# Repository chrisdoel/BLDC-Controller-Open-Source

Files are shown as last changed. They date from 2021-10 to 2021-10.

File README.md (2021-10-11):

# BLDC-Controller-Open-Source
An Open Source BLDC motor speed controller, created from scratch, which supports both sensored and sensorless motors. The full schematic, hardware, code and documentation has been provided.

# Please refer to [Documentation.pdf](/Documentation.pdf) for the complete documentation, theory behding the BLDC controller and construction instructions

# The Schematic
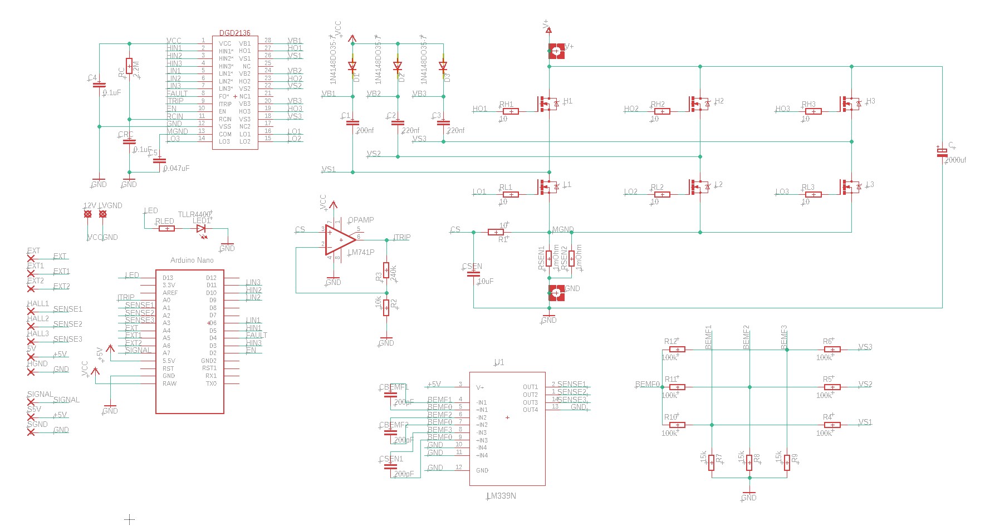
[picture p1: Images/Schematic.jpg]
Schematic
 

# An assembled BLDC controller
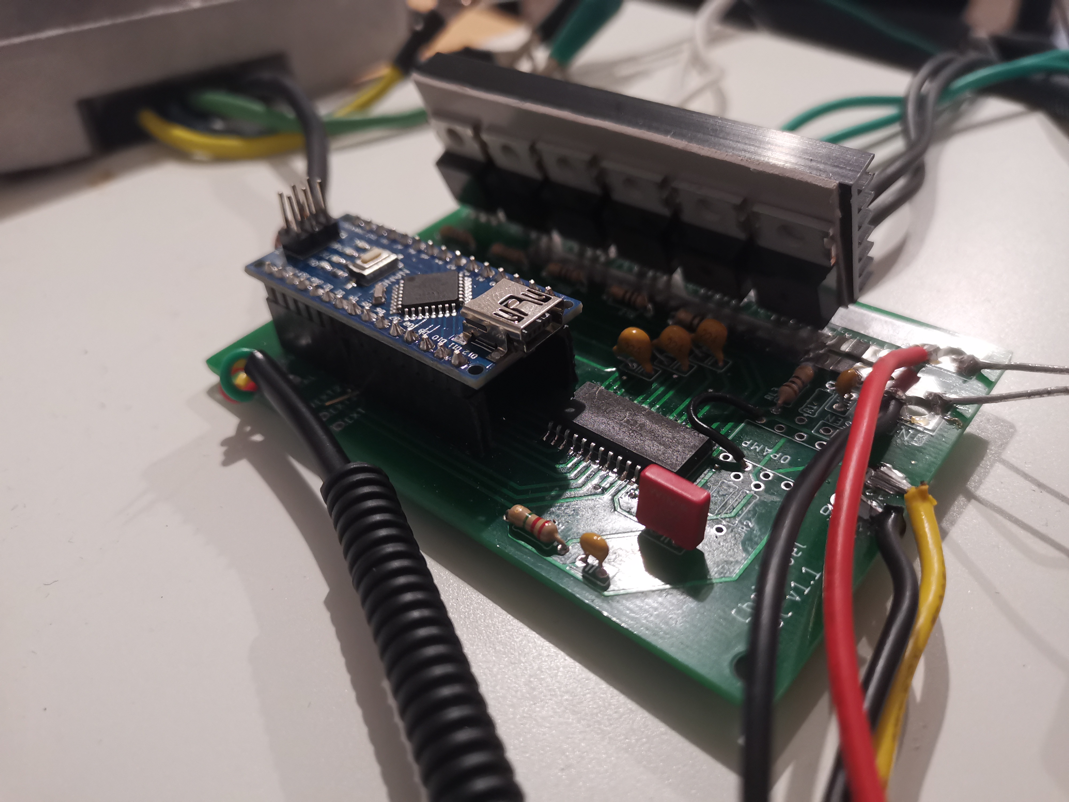
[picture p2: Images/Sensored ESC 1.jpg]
Assembled BLDC controller
 
 
 # The PCB
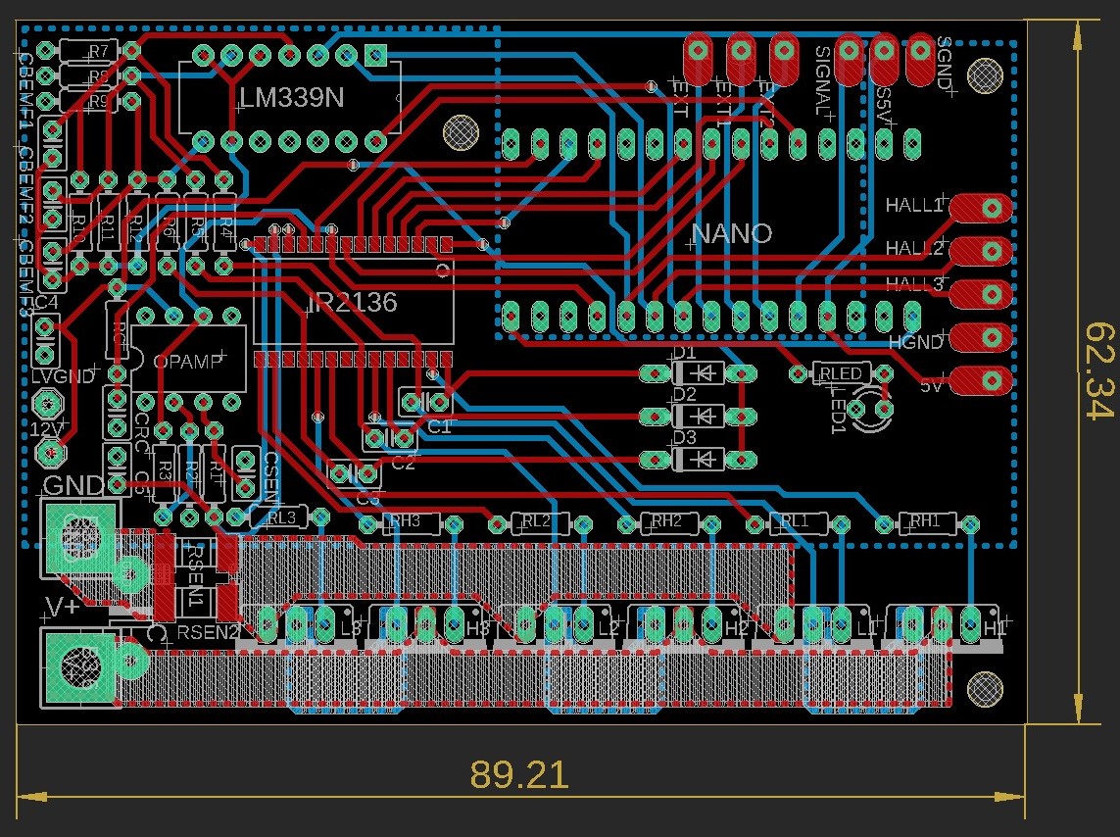
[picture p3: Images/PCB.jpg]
 
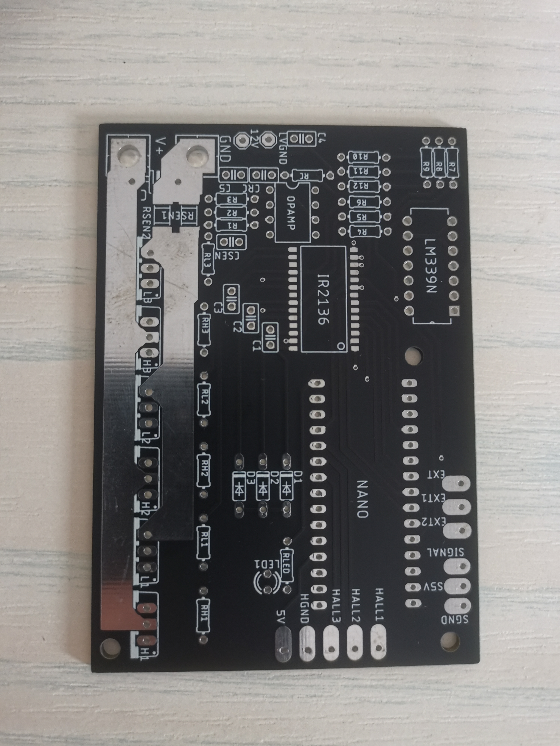
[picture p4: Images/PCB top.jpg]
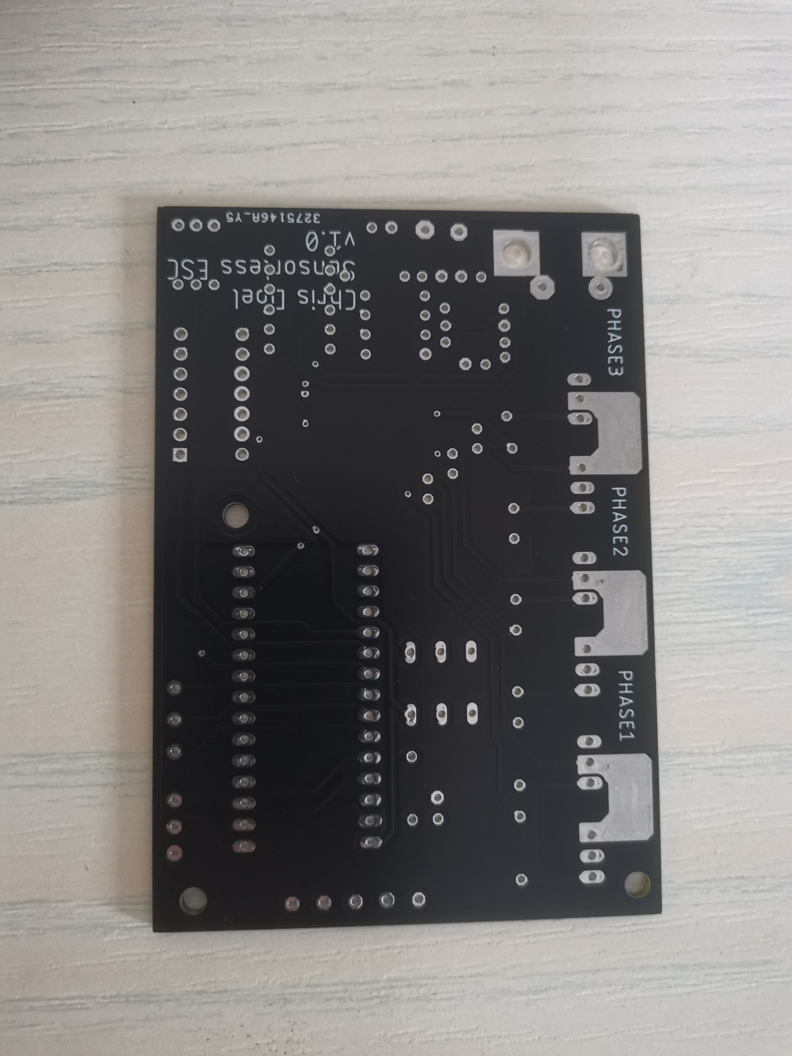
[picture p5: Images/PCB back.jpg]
|  |  |
|:---:|:---:|

# A large sensored motor setup being driven by two BLDC controllers
https://user-images.githubusercontent.com/70950249/136831820-4237cd56-f56c-432a-8c37-596cbc5fa2e3.mp4

# A sensorless motor being driven by the BLDC controller
https://user-images.githubusercontent.com/70950249/136831950-987a125a-ef0f-476e-b4f4-f5f6af1766f3.mp4

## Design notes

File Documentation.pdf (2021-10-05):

## Contents

Designing an open-source brushless motor controller, supporting sensored and sensorless

## Designing an open-source brushless motor controller, supporting sensored and sensorless commutation

Brushless motors are a form of synchronous motors which allow its permanent magnet rotors to rotate without the use of brushes. This therefore enables them to be highly efficient, have a long lifespan and have an impressive weight to power output ratio. However, the drawback of using such motors is that they cannot be powered as simply as brushed dc motors, in which a dc power supply is applied across the motor’s terminals. Brushless motors require a complicated controller,
commonly referred to as an ESC (Electronic speed controller), in order to sequentially switch dc currents across the motors three windings at specific times in order to rotate the motor. Fortunately, due to the widespread availability and cost reduction of microcontrollers and MOSFETS, brushless motor controllers have never been more accessible, especially for hobbyists.

In this documentation I will explain the design decisions and considerations of brushless motor controller with the following requirements:

- It will support sensored commutation by enabling a brushless motor’s hall sensors to be utilised to sense the rotor’s current rotation.
- It will support sensorless commutation by detecting the back EMF generated by the motor windings in order to determine the rotation of the motor’s rotor.
- It will support of an input voltage up to 42v, allowing up to a 10s lithium battery to be used.
- It will support a maximum instantaneous discharge current of around 70 amps.
- It will support a continuous discharge of 30 amps.
- Most of the components will be through hole, enabling a novice electronics hobbyist to easily construct the motor controller.
- The speed controller will be cheaper than most commercial alternatives offering the same specifications (especially when the parts are ordered from Chinese distributors).

## Hardware

### The schematic

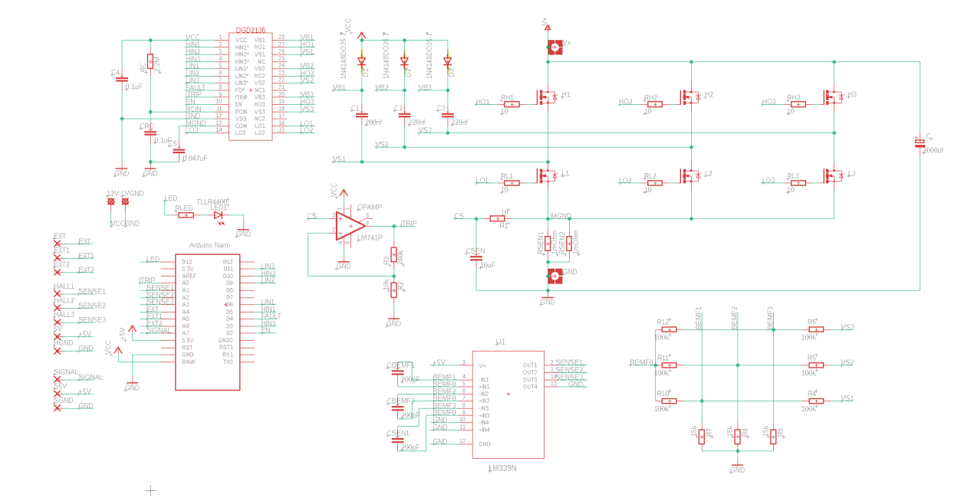
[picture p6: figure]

The speed controller’s schematic can be observed in Figure 1. This includes all the components that will be used in order to construct the speed controller, however certain components can be omitted if only sensored commutation is required (this will be discussed later in the documentation). The schematic consists of four primary areas:

- The microcontroller (an Arduino Nano)
- The triple half bridge MOSFET driver IC (an IR2136 or DGD2136)
- The triple half bridge MOSFET configuration
- The back EMF detection circuitry

### The Tripple half bridge MOSFET configuration

This arrangement of the MOSFETs enables any one of the three motor’s phases to be connected to either the supply voltage or to ground. By connecting one of the phases to the supply, and another to ground, a current is conducted through specific motor windings in a specific direction. The energised windings subsequently apply a force to the motor’s rotor through an attraction/repulsion force with the rotor’s permanent magnets.

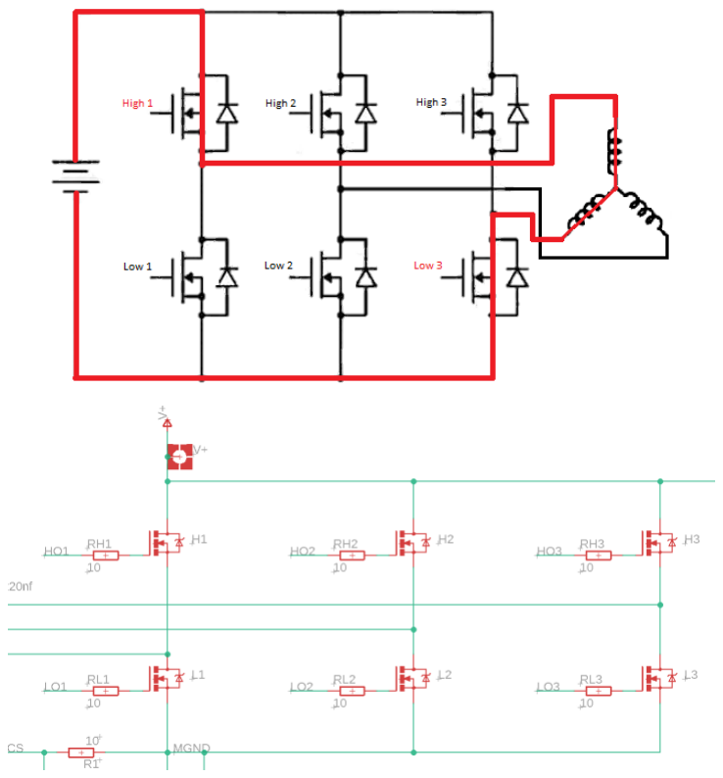
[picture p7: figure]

The MOSFET of choice is the IRF3205. This MOSFET boasts a maximum drain-source voltage of 55v and a maximum continuous drain current of 98A. This MOSFET subsequently supports our voltage requirement of 42v and can handle high continuous currents as long as the MOSFETs are sufficiently cooled.

6 step commutation
In order for a brushless motor to spin most efficiently, the motors windings must be energised in a specific order, and at specific times. This ensures that the motors torque is largest and that the current direction of rotation is maintained. The windings to be energised in order for a four-pole motor to rotate anti-clockwise can be observed in Figure x.

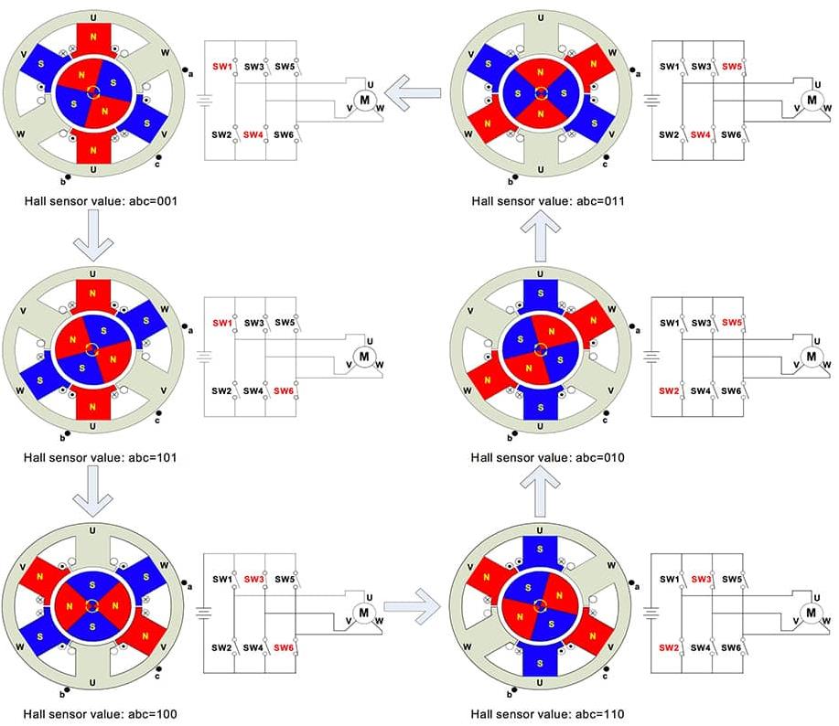
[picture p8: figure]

Figure 1 https://www.digikey.com/en/articles/how-to-power-and-control-brushless-dc-motors

Figure x demonstrates that there are 6 combinations of two MOSFETS to be activated in order for one electrical revolution to be performed (a half revolution for a 4-pole motor). Therefore, if these 6 steps are repeated, the rotor will continuously rotate. In order to adjust the speed of the motor’s rotation, a PWM waveform can be applied to the MOSFETs. The motor’s speed will adjust proportionally to the duty cycle applied to the MOSFETs; which is due to the fact that a motors speed is proportional to the average voltage applied across the motors windings.

Sensored commutation theory
As explored above, the position of the motor’s rotor is required in order to determine the two MOSFETs to be switched. One common approach of detecting the rotor’s current rotation is through the use of hall sensors integrated within the motor. These hall sensors are spaced either 60 or 120 degrees around the motors stator and detect the presence of the magnetic field from the motor’s rotor. The majority of the hall sensors output a 5v logic signal in order to indicate the magnetic pole that is present. These hall sensors are strategically spaced in order to output three logic signals which correlate to the windings that need to be energised in order to continue the motors rotation. A table showing the windings to be excited with the corresponding hall signals can be observed in Figure x.

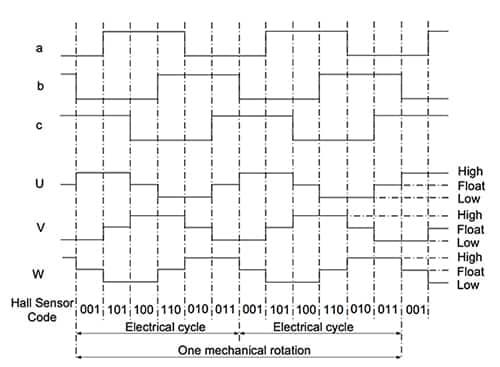
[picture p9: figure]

Sensorless commutation theory
The sensored approach highlighted above however has the disadvantage of adding additional cost and complexity to the motor. To mitigate this downside, an alternative method of detecting the motors rotation has been devised and is used extensively with hobbyist motors. This sensorless commutation approach relies on the fact that as the rotor rotates after a current is applied to two of the motor’s phases, the rotors permanent magnets pass by the motors un-excited winding. This action of passing a permanent magnet near a winding results in the generation of an EMF. As this winding is currently un-energised, the EMF can be sensed by the speed controller and can be correlated to the current position of the rotor. The waveform generated by the back EMF can be observed in Figure x below:

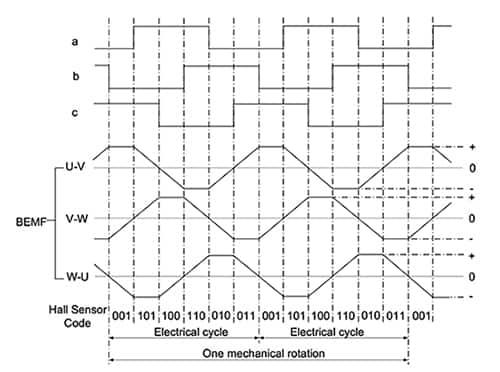
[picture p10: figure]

This diagram demonstrates that the step of the 6-step commutation is to be advanced when the BEMF of the floating phase crosses the zero point. Subsequently, this zero-crossing event can be monitored for each specific step of the 6-step commutation in order to continuously rotate the rotor.

This commutation method however consists of its own downsides. The primary downside is that the magnitude of the BEMF waveform is proportional to the rate of change of the magnetic field across the motors winding. This therefore means that at a low rotational speed, the BEMF waveform is hard to detect; and at a standstill there is no BEMF waveform at all. Therefore, the windings need to be initially energised in a sequence that is not correlated to the rotors position, until enough movement is created for a BEMF signal to be observed.

Current sensing
In order for the current draw of the BLDC controller to be measured, a shunt resistor is utilised. The voltage across this shunt resistor is amplified and measured in order to accurately determine the amount of current passing through the motor. This ensures that in situations in which the motor has stalled or is drawing more current than the BLDC controller is designed for, the PWM signal applied to the MOSFETs can be stopped in order to prevent damage. A simple non-inverting amplifier allows the small voltage across the shunt resistor to be amplified to a more appropriate voltage range for interpretation for a microcontroller or IC.

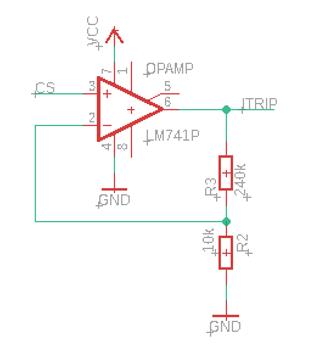
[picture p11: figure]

### Bootstrapping

Theory
Each half bridge utilises two N channel MOSFETs. Initially it may seem counter intuitive to utilise two N channel FETs due to the fact that the high side MOSFET would need a very high gate voltage, relative to the circuits ground, in order to sufficiently activate the MOSFET. This is due to the fact that there will be a voltage across the motor’s windings, therefore the high side MOSFET will require a Vgs (with respect to ground) which is equal to the MOSFETS saturation voltage plus this voltage drop across the windings. Therefore, the high side MOSFETs gate voltage must be higher than its drain voltage, meaning that this voltage will most likely have to be provided from a source external to this circuit. An alternative to using two N channel MOSFETs would be to use an N channel for the low side MOSFET and a P channel for the high side. However, using only N channel MOSFETs not only reduces the cost of the circuitry, but it also results in a reduction of the losses due to the inherent attribute of P channel MOSFETs consisting of a higher Rdson resistance.

A solution which enables the utilisation of two N channel MOSFETs in a half bridge configuration is referred to as MOSFET bootstrapping. Bootstrapping enables a capacitor, connected between the circuits supply and the high side MOSFETs drain, to be charged when the low side MOSFET is activated. The voltage across this charged capacitor can then be used in order to provide a sufficient voltage (relative to the high side MOSFETs source) to the gate of the high side MOSFET.

Implementation

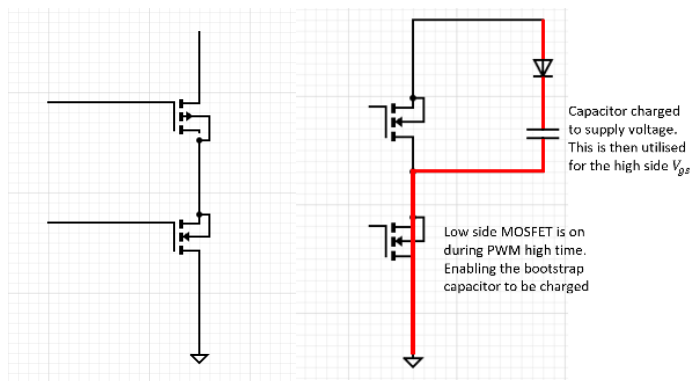
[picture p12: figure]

An 1N1418 diode has been used as the bootstrap diode due to its high speeds; this is necessary as the bootstrap capacitor will need to be sufficiently charged within the very small timeframe of the low side MOSFETs PWM on time.

A specific bootstrap capacitance is required to be tailored around the PWM frequency used to drive the MOSFETS and the MOSFETS gate capacitance.

The charge that must be stored by the bootstrap capacitor is expressed in the following equation:

QCB = QG + (tLmax × IB)

Where:

- QCB is the total charge to be stored.
- QG is the MOSFETs typical gate capacitance.
- tLmax is the maximum time that the high side MOSFET PWM waveform will be high.
- IB is the maximum quiescent supply current stated in the MOSFET driver’s datasheet.

In the case of this speed controller:

- The IRF3205 has a gate charge of 146nC, therefore QCB = 146nC
- A 31kHz PWM frequency is utilised so tLmax = 32μs

- The IR2136’s maximum quiescent Vbs supply current is IB = 70 × 10⁻⁶

QCB = 147 × 10⁻⁹ + (32 × 10⁻⁶ × 70 × 10⁻⁶

) = 1.4924 × 10⁻⁷

Finally, we need to tailor the value of CB around the maximum allowable ripple. In this case I will allow a 5% ripple of the 12v supply.

CB ≥

QCB
∆V
1.4924 × 10⁻⁷
∆V

= 248 nF

### The MOSFET driver IC

The IR2136 enables the Arduino’s 6 PWM signals to be utilised in order to switch the 6 MOSFETs within the triple half bridge configuration. Using a MOSFET driver is preferable to simply using the Arduino’s logic level PWM signals due to the fact that the Arduinos low voltage and high impedance output results in considerably slower switching times, consequentially causing MOSFET heat losses. This IC supports a supply voltage of 10-20v; I will be powering it used an automotive switching dc regulator with an output of 12v.

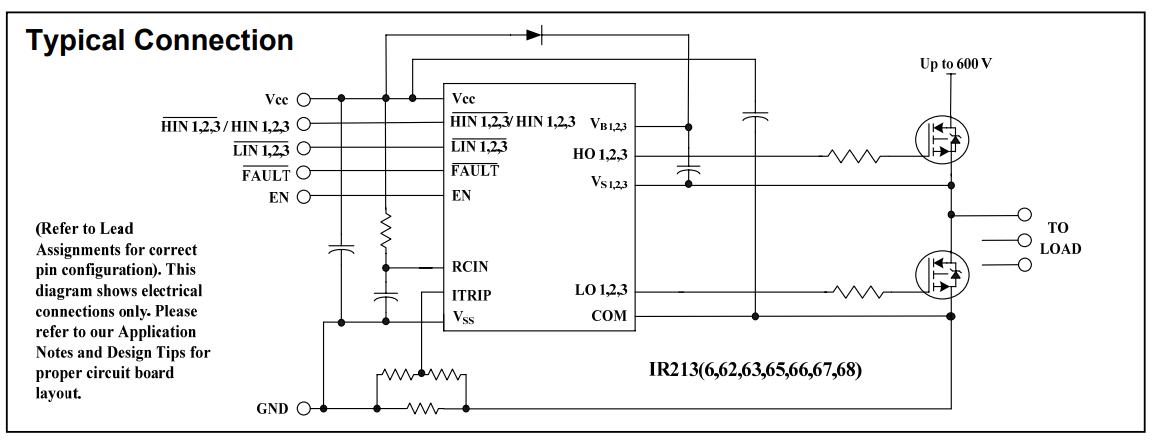
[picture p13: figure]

Pin descriptions
Pins
HIN1, 2, 3 LIN1, 2, 3 | The HIN pins receive the PWM signal for the high side MOSFETs of each half bridge and the LIN pins receive the PWM signals for the low side FETs. Depending on the variant of the ir2136, these inputs can be inverted. In my case I am using the ir2136S which has both the HIN and LIN signals inverted.
FAULT | The fault pin indicates an overcurrent or undervoltage event in the form of an open drain signal. This is connected to the Arduinos digital input pin 4 which is in pullup mode. The fault signal is inverted.
RCIN | A pin which connects to a series RC network in order to define the amount of time for the FAULT signal to clear. This time is approximately equal to R*C.
ITRIP | This is the analog input for the overcurrent detection. When the voltage at this pin exceeds 4.3V the chips operation is halted and the FAULT signal output. For this application a simple amplifier is used in order to amplify the voltage drop across the shunt resistor. The gain of the amplifier is strategically chosen in order to result in a 4.3v output when the maximum current is reached.
EN | A logic input to enable the ir2136 to operate.

HO1, 2, 3 LO1, 2, 3 | The output pins in order to drive the high and low side MOSFETs. This output logic signal will consist of the same PWM waveform applied to its corresponding input pin, however depending on the ir2136 variant it may be inverted.
VB1, 2, 3 VS1, 2, 3 | The VB pin connects to the node attaching the bootstrap capacitor to the supply voltage. The VS pin connects to the node connecting the bootstrap capacitor to the drain of the high side MOSFET. These pins enable the bootstrap capacitor to be charged and discharged in order to drive the high side N channel MOSFET.

Deadtime
The IC provides a typical dead time value of 290 nanoseconds. This means that there will be a 290ns delay between one of a half bridges MOSFETs being turned off and the other MOSFET being turned on. This minimises the risk of both MOSFETs being activated at the same time, which would result in a direct short circuit between the supply and ground through both MOSFETs.

### Sensorless commutation hardware

An effective but simple method of measuring the BEMF zero crossing events (highlighted in Sensorless Commutation Theory) is to use a resistor network composed of nine resistors, this can be observed in the Figure below.

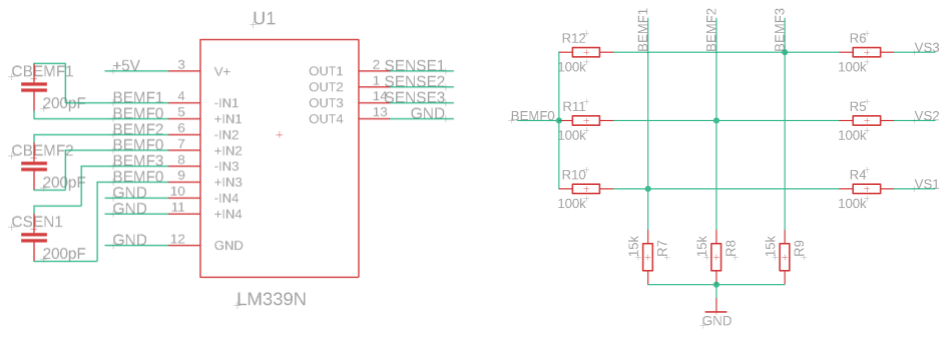
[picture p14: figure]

Resistors R6, R5 and R4 are connected to the three motor phases. R7, R8 and R9 create a potential divider with R6, R5 and R4, allowing the voltage from each phase to be attenuated to within a 5-volt range. The attenuated voltages are then combined at the BEMF0 node in order to simulate the motors neutral point (a point where a brushless motors phases join internally when in a Y configuration but is usually inaccessible externally). This point now allows us to sense the voltage across each of the motors windings by measuring the phase voltage to this virtual neutral point. This subsequently means that the BEMF induced within the motor’s windings can be detected. As we are only concerned as to whether a BEMF zero crossing event has occurred, an LM339N 4 channel comparator has been utilized. This comparator outputs a logic signal corresponding to whether the voltage across a phase winding is above or below the virtual neutral voltage. Therefore, by inspecting these signals for a change in states, we can determine that a BEMF crossing event has occurred for a particular phase, and therefore advance the commutation sequence step.

A capacitor is required in order to smooth each attenuated voltage signal in order to reduce any high frequency noise superimposed on the BEMF signal. Any superimposed noise can cause lots of bouncing and erroneous state changes to be detected. This capacitor is connected between the virtual neutral point and each of the phases and consists of a value of 200 pF.

### The microcontroller

The brains of the speed controller are in the form of an Arduino Nano, which is a breadboard-friendly board based on the ATMega328 microcontroller. These boards are widely used within the hobbyist electronic space and are incredibly cheap, especially when purchased in the form of a third-party clone. This microcontroller typically runs at 16MHz which is relatively slow compared to other microcontrollers used to control BLDC speed controllers. Therefore, the nano must be programmed as efficiently as possible to make use of the limited processing power. As a result, most of the advantages provided by the Arduino framework are not utilised and port/register manipulation was an effective programming tool.

Timer utilisation and timekeeping
The ATMega328 only has three hardware timers, all of which are used to generate the PWM signal for two of the 6 PWM pins. As the BLDC controller requires 6 PWM signals to the MOSFETs, all of the timers were already being used and therefore I could not have a timer dedicated to the task of timekeeping. The PWM frequency is set to 32kHz, and the timer resolution restricted to 8 bits, subsequently meaning that the timers value would increment and overflow extremely fast, far too fast to utilise the timer’s values for timekeeping. This issue was mitigated by adding an overflow interrupt to one of the timers, in which a global 16-bit integer is incremented at each overflow event, resultantly giving me a 32kHz timer. This timer variable would take around two seconds to overflow which is a perfectly reasonable time range.

The main requirement for timekeeping is so that there is a timeout for the speed controller being in one of the commutation steps. If the controller is in one of the commutation steps for an unordinary amount of time, then this suggests that the motor has stalled, or some other fault has occurred. As a result, the PWM duty cycle for the MOSFETs needs to be set to 0 in order to prevent a sustained high current draw. This timeout value is set to 1072 clocks of the make-shift timer, corresponding to around 32 milliseconds.

Generating the PWM waveform
The PWM frequency used to generate the PWM waveform for the MOSFETs is 32KHz. This PWM frequency is rather high, however it means that the speed controller will happily support motors that consist of high pole counts and spin at a high RPM. By default, the Arduino supports a PWM frequency of 500hz. This frequency is far too small for this application, therefore it needed to be increased by manipulating the registers that determine the timers prescaling.

The prescaler was set to 1 and the timers resolution set to 8 bits, meaning that the overflow frequency is ¹⁶⁰⁰⁰⁰⁰⁰
256

= 62500. Phase correct PWM was then applied by manipulating the timer mode registers. This means that the timer would first increment until its maximum value before decrementing back to its lowest value, resulting in a PWM frequency of 31250. The two Output Compare Registers are then set in order to toggle the PWM pins output at each matching comparison; thus, generating a PWM waveform which can be observed in the figure below.

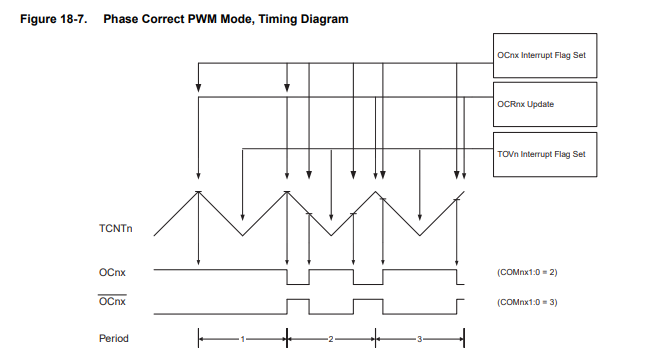
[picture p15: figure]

Sensored logic flowchart
The logic for sensored operation is rather simple. The throttle is sampled every 20 milliseconds, in which the throttle is mapped to an 8-bit range before being assigned as the PWM duty cycle. The hall sensors logic levels are read before being utilised in order to determine the commutation step that should be currently applied. A timeout is used in order to ensure that a commutation step is not applied for too long, as this suggests the motor has been stalled or the wrong commutation step is being applied.

Sensorless logic flow chart
The sensorless logic is slightly more complex. As the magnitude of the BEMF signal is proportional to the speed in which the motor is running, this means that there will not be any way to determine the rotors position while stationary. As a result, we are required to perform open loop commutation in order to get the motor to briefly move and generate a BEMF signal. As can be observed in the flowchart, the six-step commutation sequence is performed, with 5 millisecond intervals, a total of 12 times. Once this has been completed, the microcontroller attempts to detect a phase 3 BEMF event (which would be the next BEMF event to be observed). If this is successfully detected then this means that the rotors position has been determined and we can perform closed loop, sensorless commutation.

Once the rotor is spinning, the sensorless commutation is rather similar to sensored commutation. During each commutation step, the microcontroller will monitor the BEMF channels until it detects the expected rise or fall signal for that specific commutation step. This indicates that the commutation step is to be advanced, and the process is continued.

## Reflections, issues and improvements

To reflect on the speed controller as a whole, I am very satisfied with the outcome, and I believe that it meets all of my initially stated requirements. I have utilised this brushless speed controller to drive a large range of brushless motors (from small hobbyist sensorless motors to huge 1.5kW+ rated sensored motors). The sensorless commutation has greatly exceeded my expectations and is able to very reliably start and continuously rotate sensorless brusless motors. I am very pleased with the PCB and the general package of the final product, especially as the PCB is able to be utilised for both sensored and sensorless applications.

I have occasionally run into issues where two of the MOSFETs from a single phase fail and develop a short. This has only occurred when running with relatively high loads and at voltages above 36v. I believe that this issue could be a result of possibly large BEMF voltage spikes; of which are exceeding the ratings of the MOSFETs and resulting in its failure. Another possible cause of its failure could be an insufficient bootstrap capacitor, in which it is not able to contain enough charge to fully open the gate of the high side MOSFET. I will continue to investigate and rectify any issues found with this speed controller.

If I were to completely resign this speed controller then I would definitely utilise another microcontroller. As briefly explored in this documentation, the AtMega328p is not a very suitable microcontroller for this role. The primary reasoning behind this would be its limitation on speed and the availability of timers. I would also design the PCB to be able to support multiple parallel
MOSFETs for each side of each phase. Such a feature would result in a dramatic reduction of
MOSFET heating and would enable the speed controller to tolerate much higher currents. This would be due to the fact that the total MOSFET resistance would half and any heat as a result of this resistance would be distributed over multiple MOSFET packages.

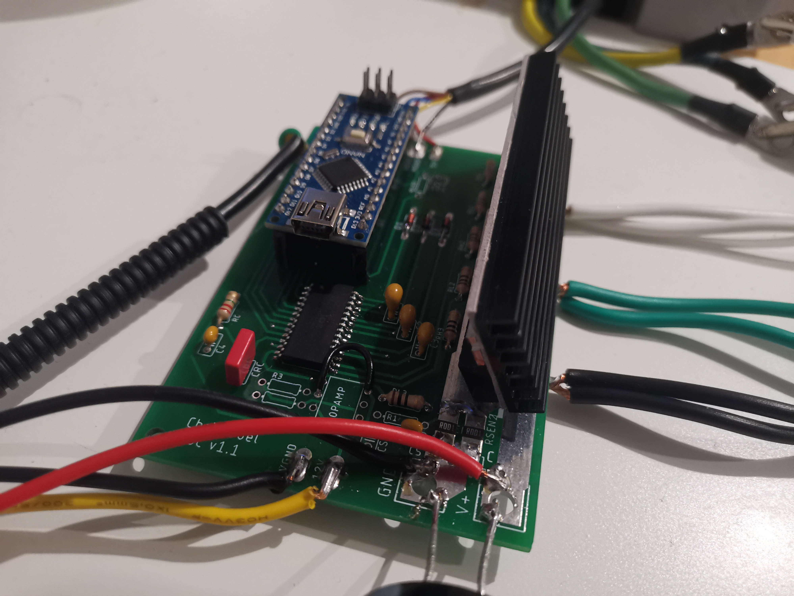
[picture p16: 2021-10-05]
Images/Sensored ESC 2.jpg

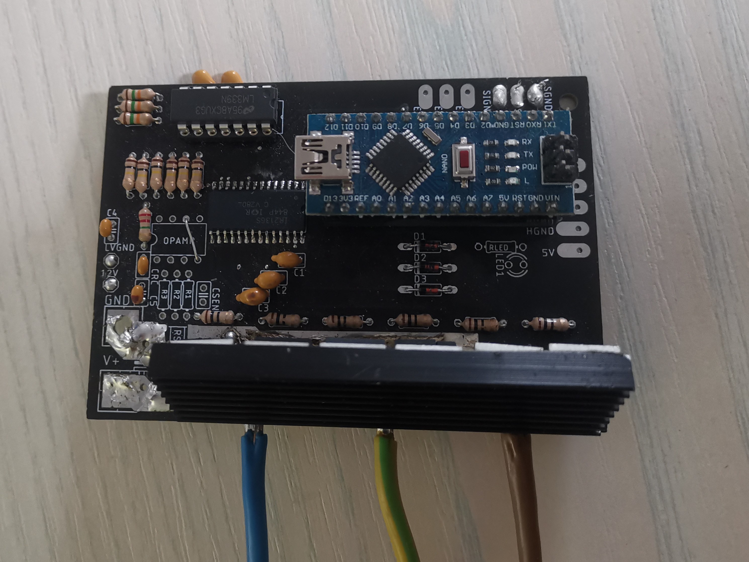
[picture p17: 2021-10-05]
Images/Sensorless ESC.jpg

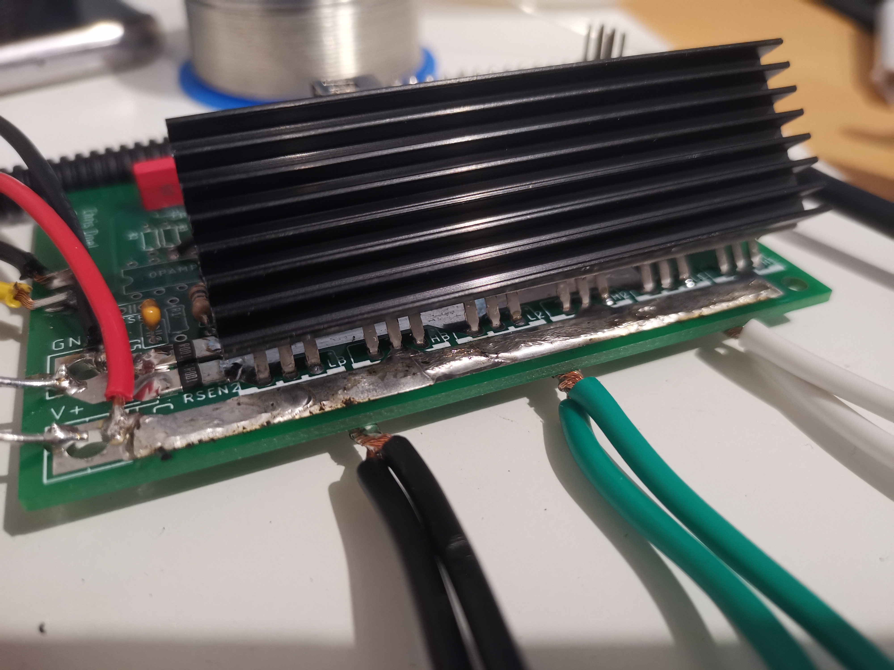
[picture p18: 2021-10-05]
Images/Copper wick added.jpg

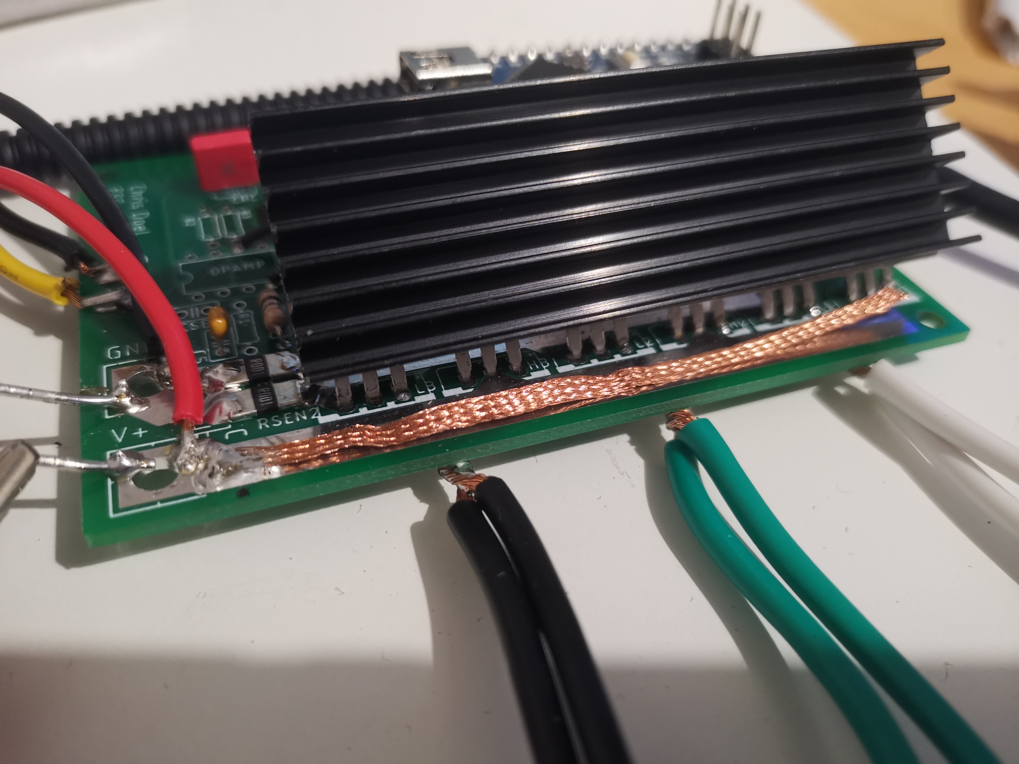
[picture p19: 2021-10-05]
Images/Adding copper wick.jpg

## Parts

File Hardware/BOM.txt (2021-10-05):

For only hall sensor operation:
1x ir2136s
6x mosfets (for cheap high current use IRF3205)
6x 10 Ohm resistor
3x 220nF (This depends heavily on the choice of mosfet and will have to be recalucated if using different mosfets, see bootstrap capacitor calculation image)
2x 0.1uf
1x 0.047uf (can be swapped for another 0.1uf)
1x 2.2M Ohm

For current limitation
2x 2512 3W 1mOhm smd resisitors
741 op amp
1x 10uf
an input and feedback resistor for required gain, for example:
>Voltage drop across the two shunt resistors in parallel at 40 amp is 40*0.0005 = 0.02v
>The ir2316 cuts out when ITRIP exceeds a voltage of 0.5v
>Therefore, if our max current was 40 amp, we want a non inverting gain of 25

Extra components for sensorless operation:
1x 10uf
3x 15k Ohm
6x 100k Ohm
1x LM339N
3x 200pf

You will obviously need an arduino nano
You will need a buck converter module capable of stepping down the input voltage to 12v and ideally able to provide 1 amp
The input is simply a potentiometer, a pulldown resistor with a high value is recommended to prevent noise being registered as throttle input if the throttle is disconnected

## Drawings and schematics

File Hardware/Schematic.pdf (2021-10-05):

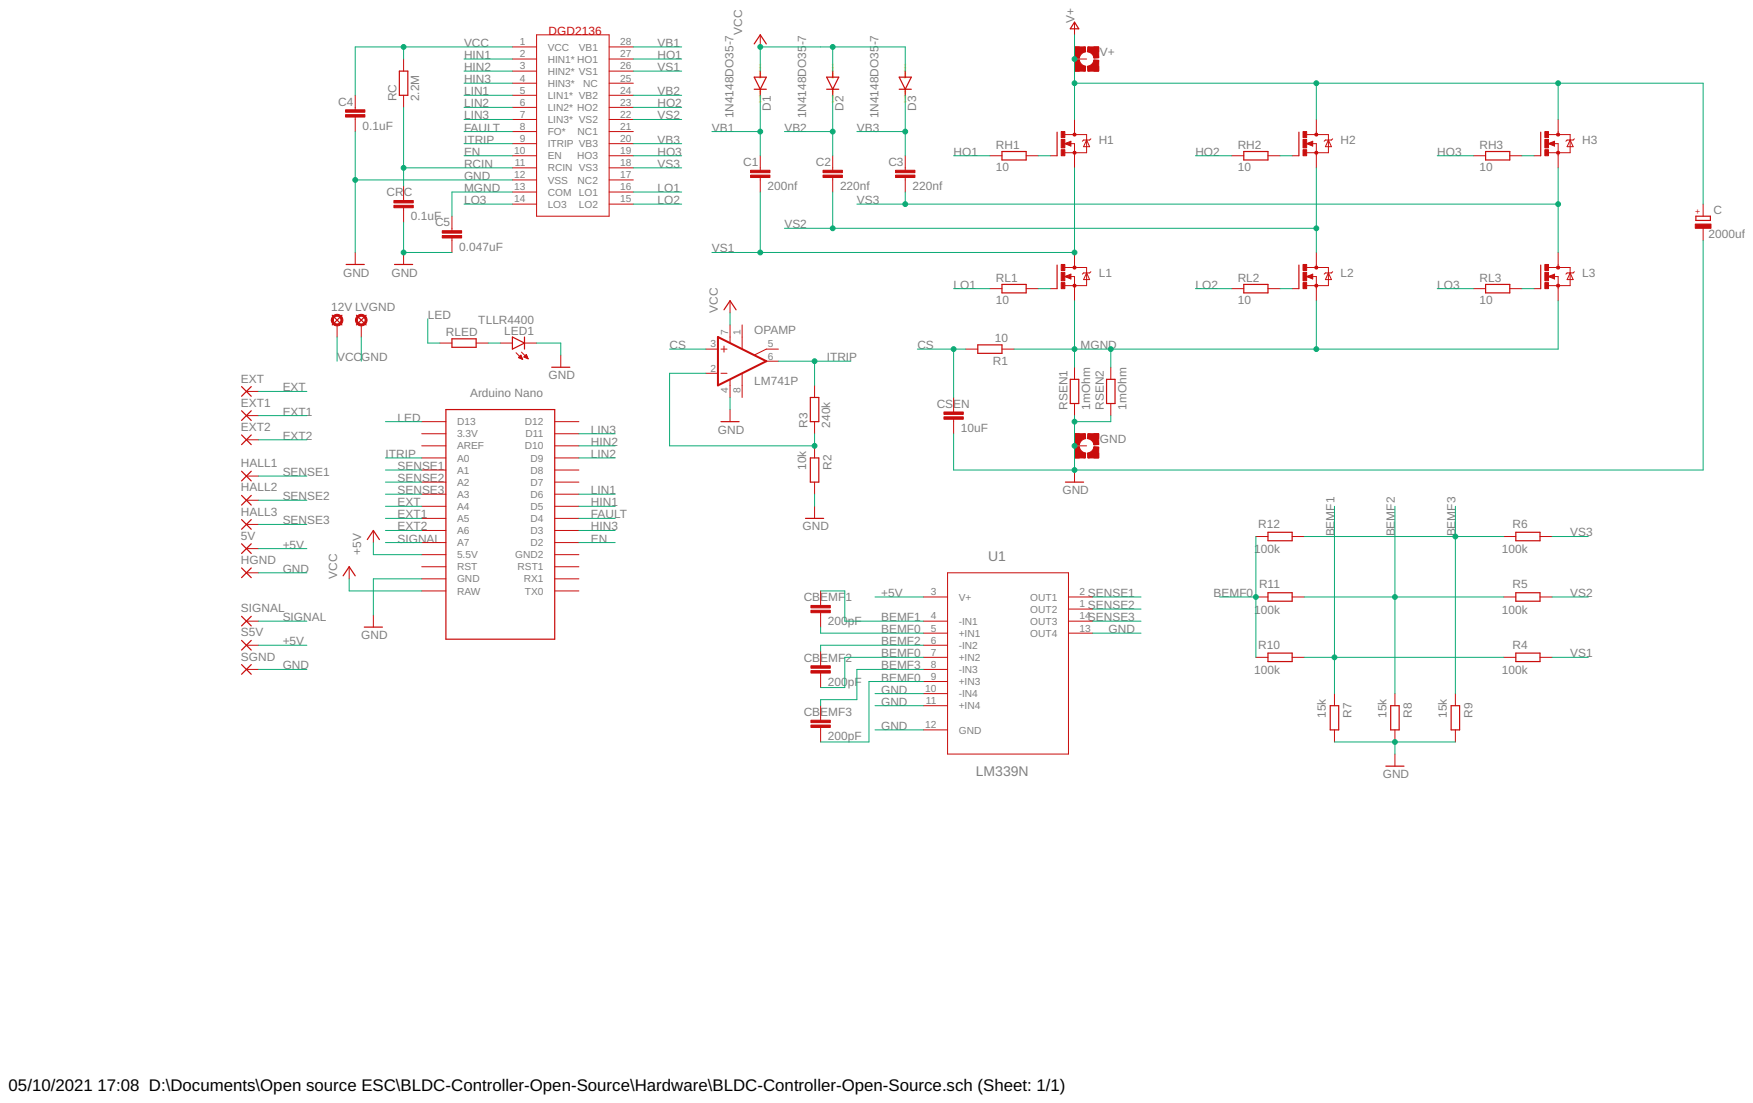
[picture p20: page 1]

05/10/2021 17:08 D:\Documents\Open source ESC\BLDC-Controller-Open-Source\Hardware\BLDC-Controller-Open-Source.sch (Sheet: 1/1)

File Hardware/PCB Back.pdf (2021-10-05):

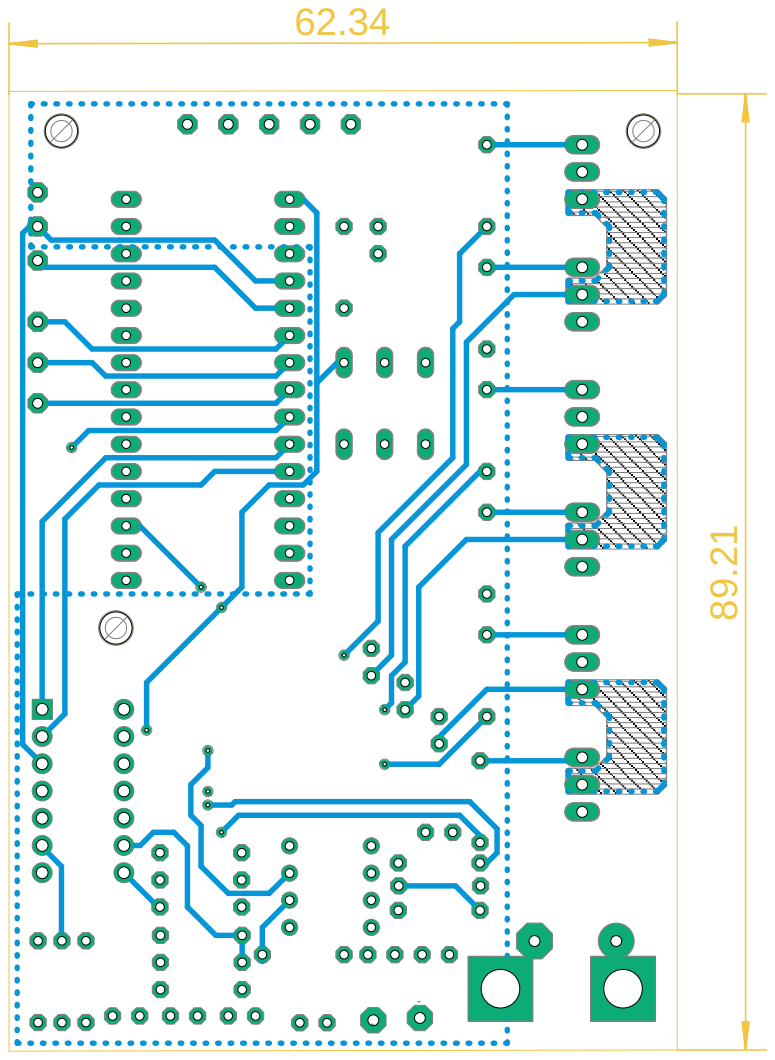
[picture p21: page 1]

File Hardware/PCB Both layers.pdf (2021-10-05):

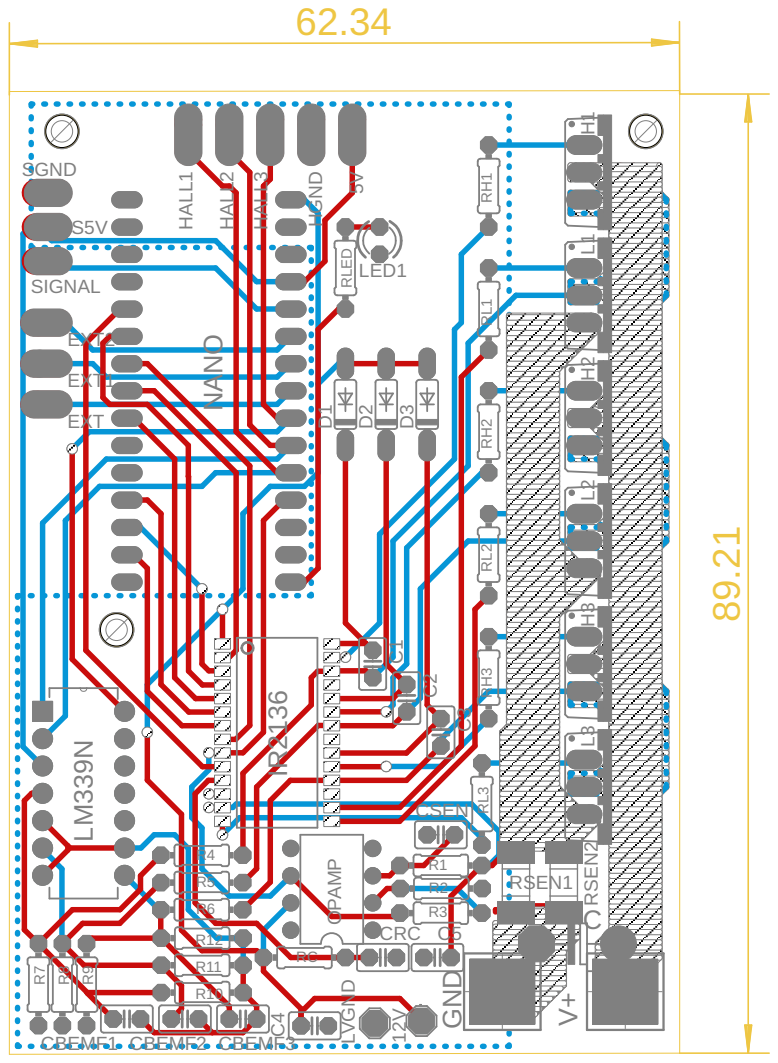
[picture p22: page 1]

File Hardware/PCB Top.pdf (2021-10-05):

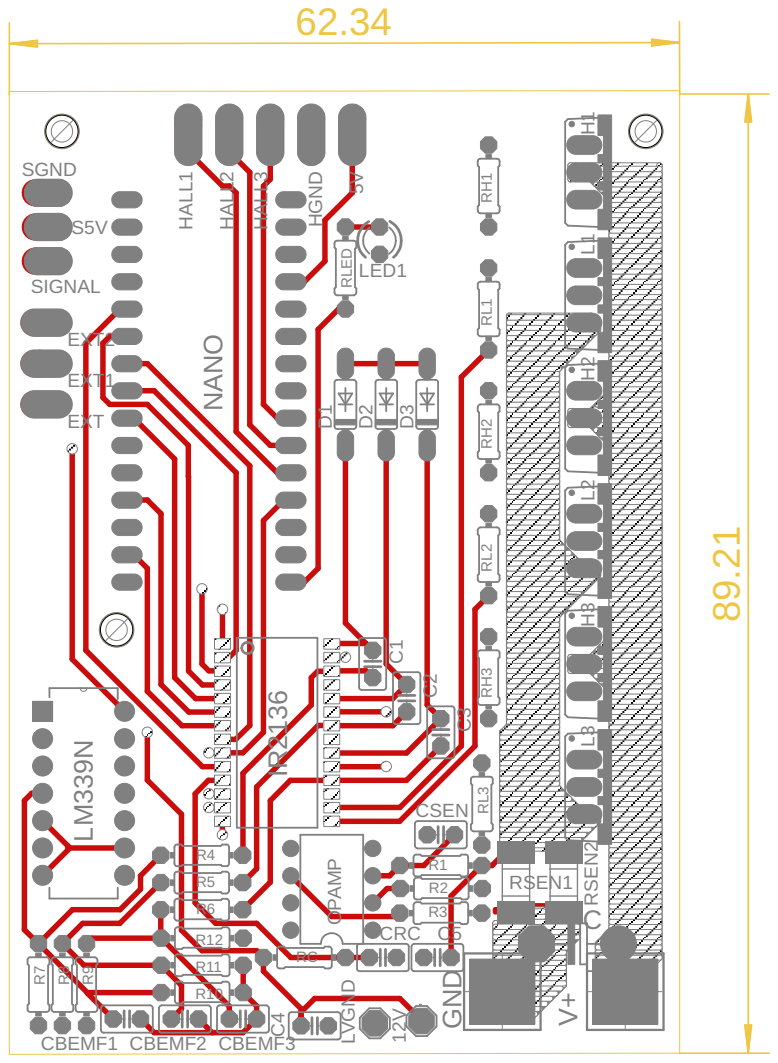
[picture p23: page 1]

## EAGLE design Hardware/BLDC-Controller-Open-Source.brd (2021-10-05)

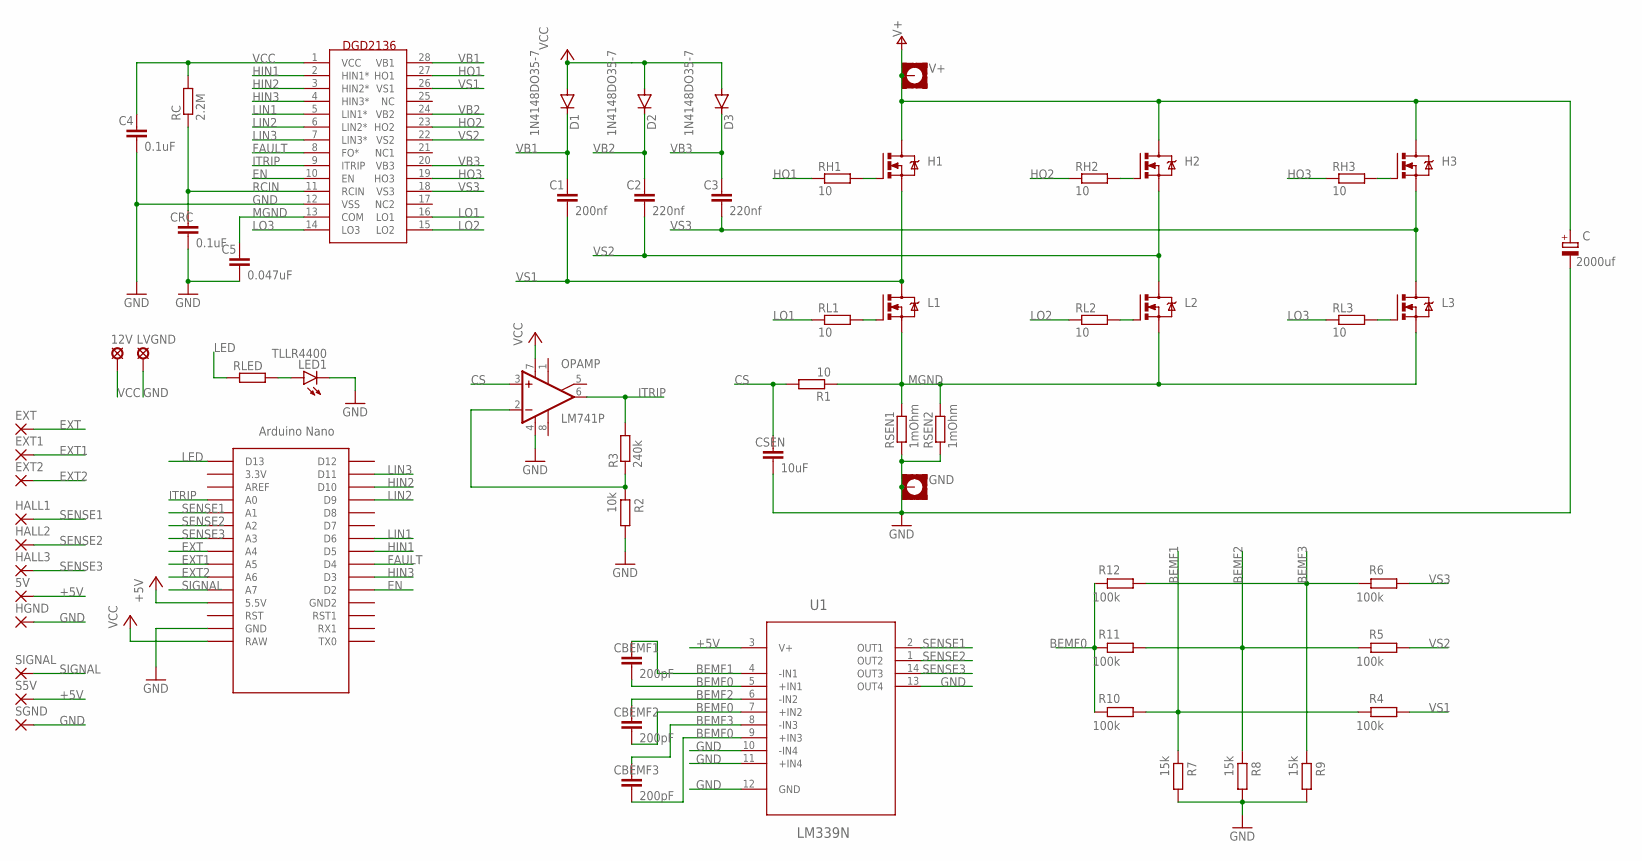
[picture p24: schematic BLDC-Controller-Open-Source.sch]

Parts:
5V: 1,6/0,9
12V: MCS10B
C: 2000uf; E7,5-16
C1: 200nf; C025-025X050
C2, C3: 220nf; C025-025X050
C4: 0.1uF; C025-025X050
C5: 0.047uF; C025-025X050
CBEMF1, CBEMF2, CBEMF3: 200pF; C025-025X050
CRC: 0.1uF; C025-025X050
CSEN: 10uF; C025-025X050
D1, D2, D3: 1N4148DO35-7; DO35-7
EXT, EXT1, EXT2: 1,6/0,9
GND: MOUNT-PAD-SQUARE3.6; 3,6-PAD-SQUARE
H1, H2, H3: IRF540; TO220BV
HALL1, HALL2, HALL3: 1,6/0,9
HGND: 1,6/0,9
L1, L2, L3: IRF540; TO220BV
LED1: TLLR4400; LED3MM
LVGND: MCS10B
OPAMP: LM741P; DIL08
R1: 10; 0204/7
R2: 10k; 0204/7
R3: 240k; 0204/7
R4, R5, R6, R10, R11, R12: 100k; 0204/7
R7, R8, R9: 15k; 0204/7
RC: 2.2M; 0204/7
RH1, RH2, RH3: 10; 0204/7
RL1, RL2, RL3: 10; 0204/7
RLED: R-EU_0204/7; 0204/7
RSEN1, RSEN2: 1mOhm; R2512
S5V: 1,6/0,9
SGND: 1,6/0,9
SIGNAL: 1,6/0,9
U1: LM339N; DIP254P762X508-14
U$1: NANO
U$2: DGD2136
V+: MOUNT-PAD-SQUARE3.6; 3,6-PAD-SQUARE

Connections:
+5V: 5V.1, S5V.1, U1.3 (V+), U$1.5V (5.5V)
BEMF0: CBEMF1.2, CBEMF2.2, CBEMF3.2, R10.2, R11.2, R12.2, U1.5 (+IN1), U1.7 (+IN2), U1.9 (+IN3)
BEMF1: CBEMF1.1, R4.2, R7.2, R10.1, U1.4 (-IN1)
BEMF2: CBEMF2.1, R5.2, R8.2, R11.1, U1.6 (-IN2)
BEMF3: CBEMF3.1, R6.2, R9.2, R12.1, U1.8 (-IN3)
CS: CSEN.1, OPAMP.3 (+IN), R1.2
EN: U$1.D2, U$2.10 (EN)
EXT: EXT.1, U$1.A4
EXT1: EXT1.1, U$1.A5
EXT2: EXT2.1, U$1.A6
FAULT: U$1.D4, U$2.8 (FO*)
GND: C.-, C4.2, C5.2, CRC.2, CSEN.2, GND.B3,6, HGND.1, LED1.K (C), LVGND.MP, OPAMP.4 (V-), R2.1, R7.1, R8.1, R9.1, RSEN1.1, RSEN2.1, SGND.1, U1.10 (-IN4), U1.11 (+IN4), U1.12 (GND), U1.13 (OUT4), U$1.GND, U$2.12 (VSS)
HIN1: U$1.D5, U$2.2 (HIN1*)
HIN2: U$1.D10, U$2.3 (HIN2*)
HIN3: U$1.D3, U$2.4 (HIN3*)
HO1: RH1.1, U$2.27 (HO1)
HO2: RH2.1, U$2.23 (HO2)
HO3: RH3.1, U$2.19 (HO3)
ITRIP: OPAMP.6 (OUT), R3.2, U$1.A0, U$2.9 (ITRIP)
LED: RLED.1, U$1.D13
LIN1: U$1.D6, U$2.5 (LIN1*)
LIN2: U$1.D9, U$2.6 (LIN2*)
LIN3: U$1.D11, U$2.7 (LIN3*)
LO1: RL1.1, U$2.16 (LO1)
LO2: RL2.1, U$2.15 (LO2)
LO3: RL3.1, U$2.14 (LO3)
MGND: C5.1, L1.S, L2.S, L3.S, R1.1, RSEN1.2, RSEN2.2, U$2.13 (COM)
unnamed: L3.G, RL3.2
unnamed: H3.G, RH3.2
unnamed: L1.G, RL1.2
unnamed: L2.G, RL2.2
unnamed: H2.G, RH2.2
unnamed: H1.G, RH1.2
unnamed: OPAMP.2 (-IN), R2.2, R3.1
unnamed: LED1.A, RLED.2
RCIN: CRC.1, RC.1, U$2.11 (RCIN)
SENSE1: HALL1.1, U1.2 (OUT1), U$1.A1
SENSE2: HALL2.1, U1.1 (OUT2), U$1.A2
SENSE3: HALL3.1, U1.14 (OUT3), U$1.A3
SIGNAL: SIGNAL.1, U$1.A7
V+: C.+, H1.D, H2.D, H3.D, V+.B3,6
VB1: C1.1, D1.C, U$2.28 (VB1)
VB2: C2.1, D2.C, U$2.24 (VB2)
VB3: C3.1, D3.C, U$2.20 (VB3)
VCC: 12V.MP, C4.1, D1.A, D2.A, D3.A, OPAMP.7 (V+), RC.2, U$1.RAW, U$2.1 (VCC)
VS1: C1.2, H1.S, L1.D, R4.1, U$2.26 (VS1)
VS2: C2.2, H2.S, L2.D, R5.1, U$2.22 (VS2)
VS3: C3.2, H3.S, L3.D, R6.1, U$2.18 (VS3)

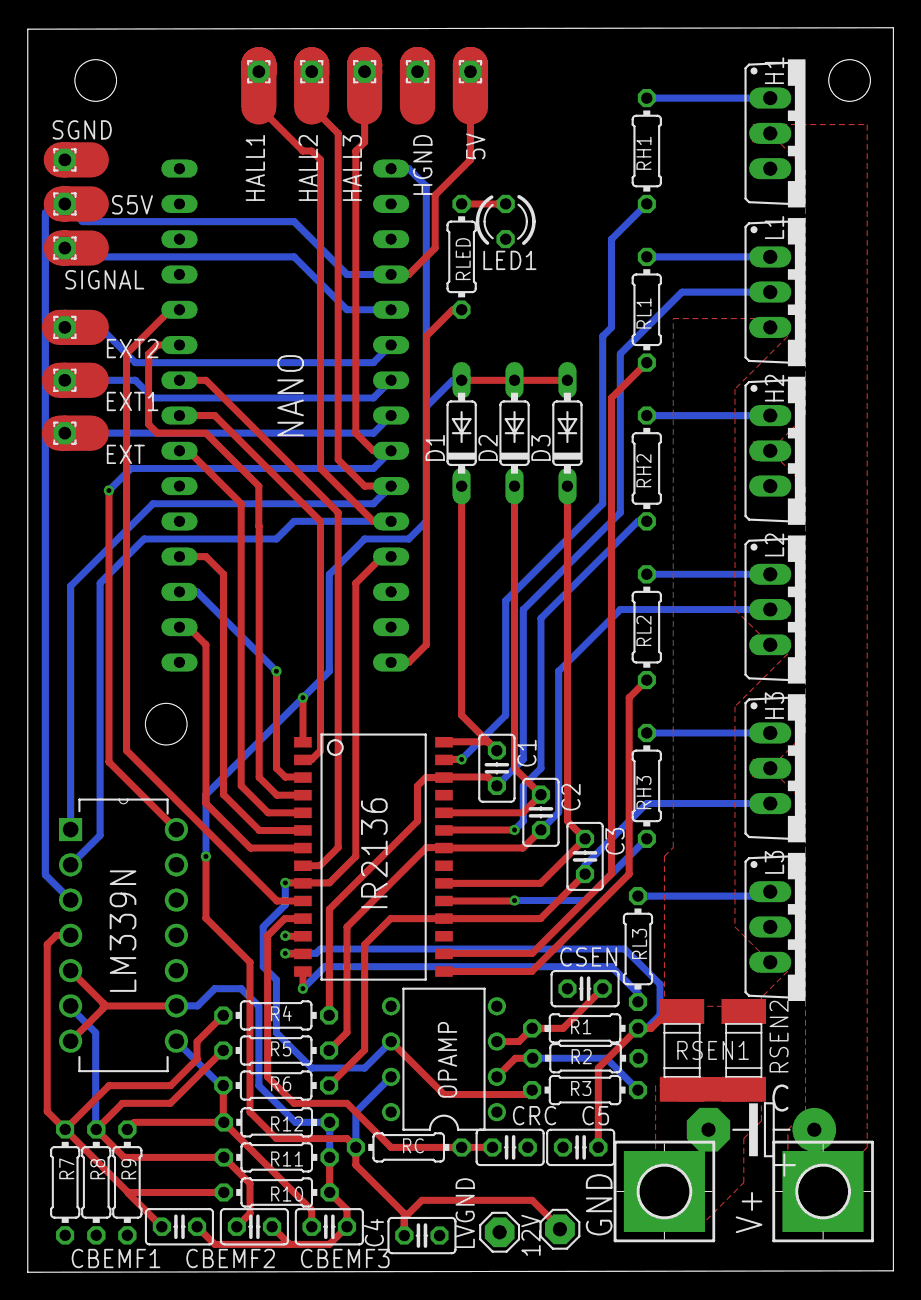
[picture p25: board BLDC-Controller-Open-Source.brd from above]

Board: 2 copper layers, 62.3 x 89.6 mm, 62 parts (0 on the bottom side), 48 nets.

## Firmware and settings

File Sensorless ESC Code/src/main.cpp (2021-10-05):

#define _DISABLE_ARDUINO_TIMER0_INTERRUPT_HANDLER_

#include <Arduino.h>
#include <wiring.c>

#define H3Pwm OCR2B
#define H2Pwm OCR1B
#define H1Pwm OCR0B

#define L3Pwm OCR2A
#define L2Pwm OCR1A
#define L1Pwm OCR0A

#define EN PORTD2

#define SENSE3 PORTC3
#define SENSE2 PORTC2
#define SENSE1 PORTC1

#define lowMax 0x00
#define lowMin 0xFF

#define highMax 0xFF
#define highMin 0x00

//Stores when the latest commutation occurred
uint16_t commutationStartTime = 0;

//Stores a 16 bit timer value, this is incremented at 31250hz
volatile uint16_t timer = 0;

//Stores a 16 bit timer value, this is incremented at 31250hz
volatile uint16_t watchdog = 0;

//Stores the last time the throttle was sampled
uint16_t lastThrottleSample = 0;

//The maximum time for a commutation change to occur before the commutation is halted (30ms)
uint16_t timeout = 1072;

//The current step of the commutation sequence
uint8_t commutation = 0;

//Whether the startup procedure has successfully been achieved
bool running = 0;

//The PWM duty cycle to apply to the mosfets
uint8_t pwmVal = 0;

//The intensity of regenerative braking
uint8_t brakeIntensity = 20;

uint16_t currentThrottle = 0;

//Amount of change to apply to the pwm value at 50hz
//This will be used for artificial acceleration to ensure power is not applied too quickly
uint8_t throttleAcceleration = 2;

//There are only 6 timers, of which all are utilised for PWM.
//Therefore a "software timer" has been made by incrementing a
//variable at the overflow of one of the timers.
//Resulting in a 31.25kHz timer
ISR (TIMER0_OVF_vect){
  timer++;
  watchdog++;
}

//Disable all PWM output to mosfets
void COMMDisable(){
  L1Pwm = lowMin;
  L2Pwm = lowMin;
  L3Pwm = lowMin;

  H1Pwm = highMin;
  H2Pwm = highMin;
  H3Pwm = highMin;
  currentThrottle = 0;
}

void COMM0(uint8_t pwm){
  if(pwmVal)
    L1Pwm = lowMin;
  else
    L1Pwm = lowMin - brakeIntensity;
  L2Pwm = lowMax; //L2 On
  L3Pwm = lowMin;

  H1Pwm = pwm; //H1 On
  H2Pwm = highMin;
  H3Pwm = highMin;
}

void COMM1(uint8_t pwm){
  if(pwmVal)
    L1Pwm = lowMin;
  else
    L1Pwm = lowMin - brakeIntensity;
  L2Pwm = lowMin;
  L3Pwm = lowMax; //L3 On

  H1Pwm = pwm; //H1 On
  H2Pwm = highMin;
  H3Pwm = highMin;
}

void COMM2(uint8_t pwm){
  L1Pwm = lowMin;
  if(pwmVal)
    L2Pwm = lowMin;
  else
    L2Pwm = lowMin - brakeIntensity;
  L3Pwm = lowMax; //L3 On

  H1Pwm = highMin;
  H2Pwm = pwm; //H2 On
  H3Pwm = highMin;
}

void COMM3(uint8_t pwm){
  L1Pwm = lowMax; //L1 On
  if(pwmVal)
    L2Pwm = lowMin;
  else
    L2Pwm = lowMin - brakeIntensity;
  L3Pwm = lowMin;

  H1Pwm = highMin;
  H2Pwm = pwm; //H2 On
  H3Pwm = highMin;
}

void COMM4(uint8_t pwm){
  L1Pwm = lowMax; //L1 On
  L2Pwm = lowMin;
  if(pwmVal)
    L3Pwm = lowMin;
  else
    L3Pwm = lowMin - brakeIntensity;

  H1Pwm = highMin;
  H2Pwm = highMin;
  H3Pwm = pwm; //H3 On
}

void COMM5(uint8_t pwm){
  L1Pwm = lowMin;
  L2Pwm = lowMax; //L2 On
  if(pwmVal)
    L3Pwm = lowMin;
  else
    L3Pwm = lowMin - brakeIntensity;

  H1Pwm = highMin;
  H2Pwm = highMin;
  H3Pwm = pwm; //H3 On
}

bool checkRise(uint8_t port){
  uint8_t total = 0;
  for(int i = 0; i < 10; i++) //Sample the pin 10 times to prevent false positives 
    total += (PINC >> port) & 1;
  if(total == 10) //If all 10 samples were high then we can assume a transition has occurred
    return true;
  return false;
}

bool checkFall(uint8_t port){
  uint8_t total = 0;
  for(int i = 0; i < 10; i++) //Sample the pin 10 times to prevent false positives 
    total += (PINC >> port) & 1;
  if(total == 0) //If all 10 samples were low then we can assume a transition has occurred
    return true;
  return false;
}


bool startup(){
  uint8_t startupPower = 30; //The PWM duty cycle to apply during startup

  uint16_t commutationDelay = 144; //The number of ticks at 31.25khz for each commutation time
  uint16_t accelleration = 0; //The reduction to apply to commutationDelay after each commutation step
  uint8_t commutationChanges = 0;
  uint8_t commutationIterations = 12; //How many commutation steps to perform

  commutationStartTime = timer;
  commutation = 0;
  COMM0(startupPower);

  while(commutationChanges < commutationIterations){
    //Serial.print(commutation);
    switch(commutation){
      case(0):
        if(timer - commutationStartTime > commutationDelay){ //Check if no BEMF crossing has been detected within a certian time frame
          COMM1(startupPower);
          commutationStartTime = timer; //Reset timer for BEMF crossing
          commutation = 1; //Prepare to attempt next commutation
          commutationDelay -= accelleration; //Decrease time frame for open loop BEMF commutation
          commutationChanges++;
        }
        break;
      case(1):
        if(timer - commutationStartTime > commutationDelay){
          COMM2(startupPower);
          commutationStartTime = timer;
          commutation = 2;
          commutationDelay -= accelleration;
          commutationChanges++;
        }
        break;
      case(2):
        if(timer - commutationStartTime > commutationDelay){
          COMM3(startupPower);
          commutationStartTime = timer;
          commutation = 3;
          commutationDelay -= accelleration;
          commutationChanges++;
        }
        break;
      case(3):
        if(timer - commutationStartTime > commutationDelay){
          COMM4(startupPower);
          commutationStartTime = timer;
          commutation = 4;
          commutationDelay -= accelleration;
          commutationChanges++;
        }
        break;
      case(4):
        if(timer - commutationStartTime > commutationDelay){
          COMM5(startupPower);
          commutationStartTime = timer;
          commutation = 5;
          commutationDelay -= accelleration;
          commutationChanges++;
        }
        break;
      case(5):
        if(timer - commutationStartTime > commutationDelay){
          COMM0(startupPower);
          commutationStartTime = timer;
          commutation = 0;
          commutationDelay -= accelleration;
          commutationChanges++;
        }
        break;
      default:
        COMMDisable();
    }
  }

  while((timer - commutationStartTime) < timeout){ //Observe the expected back emf after manually comutating the motor
    if(checkRise(SENSE3)){ //If a zero crossing event occurred we can start the normal commutation
      watchdog = 0;
      commutation = 1;
      COMM1(startupPower);
      Serial.println("Got BEMF");
      currentThrottle = startupPower;
      pwmVal = startupPower;
      return true;
    }
  }
  Serial.println("Couldnt start");
  return false;
}

//Commutation for when the startup procedure was successful
void activeCommutate(){
  switch(commutation){
    case(0):
      if(checkRise(SENSE3)){  //Check if the zero crossing event has occurred
        watchdog = 0; //Record the time of the zero crossing event
        commutation = 1; //Move to the next commutation step
        COMM1(pwmVal); //Set the outputs of the MOSFETs
      }
      break;

    case(1):
      if(checkFall(SENSE2)){
        watchdog = 0;
        commutation = 2;
        COMM2(pwmVal);
      }
      break;

    case(2):
      if(checkRise(SENSE1)){
        watchdog = 0;
        commutation = 3;
        COMM3(pwmVal);
      }
      break;

    case(3):
      if(checkFall(SENSE3)){
        watchdog = 0;
        commutation = 4;
        COMM4(pwmVal);
      }
      break;

    case(4):
      if(checkRise(SENSE2)){
        watchdog = 0;
        commutation = 5;
        COMM5(pwmVal);
      }
      break;

    case(5):
      if(checkFall(SENSE1)){
        watchdog = 0;
        commutation = 0;
        COMM0(pwmVal);
      }
      break;

    default:
      COMMDisable();
  }

  if(watchdog > timeout) {//Check if there has been no BEMF detected in the last 30ms
    uint16_t now = timer;
    running = false; //We can safely assume the motor has stopped rotating
  }
}

void setup() {
  noInterrupts();
  ADCSRA &= ~((1 << ADPS0) | (1 << ADPS1) | (1 << ADPS2)); //Clear ADC prescaler bits
  ADCSRA |= (1 << ADPS0) | (1 << ADPS2); //Set adc prescaler to 32 = 20 microsecond analogRead
  
  //TIMER0
  TCCR0A = 0; //Set timer0 config to 0
  TCCR0B = 0;
  //Setup Phase correct PWM
  TCCR0A |= (1 << COM0A1); //Non-inverted low side PWM
  TCCR0A |= (1 << COM0B0);
  TCCR0A |= (1 << COM0B1); //Invert High side PWM
  TCCR0A |= (1 << WGM00);
  TCCR0B = (1 << CS00); //Prescaler divided by 1, 31.37255khz frequency

  //TIMER1
  TCCR1A = 0;
  TCCR1B = 0;
  TCCR1A |= (1 << COM1A1);
  TCCR1A |= (1 << COM1B0);
  TCCR1A |= (1 << COM1B1);
  TCCR1A |= (1 << WGM10);
  TCCR1B = (1 << CS10);

  //TIMER2
  TCCR2A = 0;
  TCCR2B = 0;
  TCCR2A |= (1 << COM2A1);
  TCCR2A |= (1 << COM2B0);
  TCCR2A |= (1 << COM2B1);
  TCCR2A |= (1 << WGM20);
  TCCR2B = (1 << CS20);

   //Zero duty cycle pwm
  OCR0A = 0x00;
  OCR0B = 0x00;
  OCR1A = 0x00;
  OCR1B = 0x00;
  OCR2A = 0x00;
  OCR2B = 0x00;

  //Setup PWM output ports
  DDRB = B00001110; //Set PORTB 1, 2 and 3 to output
  DDRD = B01101100; //Set PORTD 5 and 6 to output

  //Setup throttle input port
  DDRC = B00000000; //Set PORTC to input

  //Enable interrupts
  interrupts();
  Serial.begin(115200);
  digitalWrite(2, HIGH); //Enable ir2136

  pinMode(A1, INPUT_PULLUP); //Set BEMF input pins to pull up as the lm339n is open drain output
  pinMode(A2, INPUT_PULLUP);
  pinMode(A3, INPUT_PULLUP);
}

void getThrottle(){
  uint16_t targetThrottle = analogRead(A7);

  if(targetThrottle >= 15){
    targetThrottle = map(targetThrottle, 0, 1023, 0, 255);
    if(currentThrottle < targetThrottle && uint16_t(currentThrottle) + throttleAcceleration <= 255) //Artifical acceleration applied
      currentThrottle += throttleAcceleration;
    else //Instant deacceleration
      currentThrottle = targetThrottle;
  }
  else
    currentThrottle = 0;
  pwmVal = currentThrottle;
  
  if(pwmVal < 15)//prevent pulses of less than a microsecond (specified in ir2136 datasheet)
    pwmVal = 0;
}

void loop() {
  if(timer - lastThrottleSample > 625){ //Sample the throttle at 50hz
    getThrottle();
    lastThrottleSample = timer;
  }

  if(pwmVal > 20 && !running)
    running = startup();
  else if(running)
    activeCommutate();
  else
    COMMDisable();
}

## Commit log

2021-10-05 Added example images/videos, the first iteration of the documentation, code for sensored and sensorless operation, the schematic and board files
2021-10-05 Added hardware files
    [BLDC-Controller-Open-Source.brd, BLDC-Controller-Open-Source.sch]
